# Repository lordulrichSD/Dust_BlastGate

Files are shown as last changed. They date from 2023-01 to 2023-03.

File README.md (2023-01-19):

# Dust_BlastGate

This project is a Dust collection system blast gate for woodworking or other dust collection.  The device provides control of a servo to actuate the blast gate, manual control of the blast gate position, a connector to attatch a sensor for tool activation and automatic control and wifi connection to activate a dust collector connected to a Kassa capable smart plug or switch.  

Software is seetup to allow over the air firmware updates direct from github. BoardInfo.py and Settings.py are not part of OTA update. BoardInfo.py contains hardware pinouts and should reflect hardware revisions.  Settings.py contains device configurations, i.e. wifi, servo limits, IP for dust collector and delay time.  These settings are set per device

BoardInfo files contain board specific information (i.e. pin mappings), BoardInfo must be loaded manualy at inital install and will not update OTA.  

Hardware folder contains KiCAD files for board revisions.  Boards are uploaded to OSHpark.  

Firmware folder contains the firmware.  Files except Settings.py are subject to OTA update.  

settings.py file contains example data/startup data. File will be overwritten when configuring board for the first time.  Write this file durring intial install.

Hardware
Hardware contains 2 main modules.  The main control module and sensor module.  
The main control module contains an ESP32 module (providing microcontroler and wifi connection).  In addition the main control module holds support hardware (i.e. power supply) and interface connections.  
A manual control switch (1p3t on-off-on) provides manual on, auto, manual off control.  
Dip switches provide for entering Access Point Mode for settings, enabling WIFI (when not in AP mode) enabling the sensor in put.  
A FTDI type 6 pin headder is provided for programing and debug by serial.
A 3 pin header is provided to connect a hobby servo to activate the physical blast gate
Sensor connection is via a RJ-9 Style connector to allow easy cable creation of needed lenght for indivitual physical install.  This connector includes 3.3v, ground, sensor data (logic high/low), and raw USB voltage (allowing USB power supply to be at sensor location)
A USB connetor is provided for power only.  A jumper or switch (populate 1) allowing selection of power source (one at a time, sensor or main control module)

(Future feature to deploy)
OTA updated based on ugit (https://github.com/turfptax/ugit)
https://github.com/turfptax/ugit/blob/f6872930eea33ae5fb45ea48af146518e4737e93/ugit.py

KASA integration based on the work by GadgetReactor in the pyHS100 based on the work of The communication protocol was reverse engineered by Lubomir Stroetmann and
Tobias Esser in 'Reverse Engineering the TP-Link HS110':
https://www.softscheck.com/en/reverse-engineering-tp-link-hs110/.  The HS100 or python-kasa libraries were not used directly due to memory limitations of the ESP32 module so only limited functions were recreated directly.

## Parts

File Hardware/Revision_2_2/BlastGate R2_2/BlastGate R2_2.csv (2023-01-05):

Source: | C:\Users\Catherine\Documents\BlastGate\BlastGate R2\BlastGate R2.kicad_sch
Date: | 11/16/2022 3:56:45 PM
Tool: | Eeschema (6.0.7)
Generator: | C:\Program Files\KiCad\6.0\bin\scripting\plugins/bom_csv_grouped_by_value_with_fp.py
Component Count: | 40
Ref | Qnty | Value | Cmp name | Footprint | Description | Vendor
C2, C6, C7, C9, | 4 | 0.1uf | C | Capacitor_SMD:C_1206_3216Metric_Pad1.33x1.80mm_HandSolder | Unpolarized capacitor
C3, C4, C12, C13, | 4 | 100uf | C_Polarized | Capacitor_THT:CP_Radial_D5.0mm_P2.50mm | Polarized capacitor
C5, C8, C10, | 3 | 1000uf | C_Polarized | Capacitor_THT:CP_Radial_D12.5mm_P5.00mm | Polarized capacitor
C11, | 1 | 1uf | C | Capacitor_SMD:C_1206_3216Metric_Pad1.33x1.80mm_HandSolder | Unpolarized capacitor
D1, D2, D3, D4, D5, | 5 | LED | LED | LED_SMD:LED_1206_3216Metric_Pad1.42x1.75mm_HandSolder | Light emitting diode
D6, | 1 | D | D | Diode_THT:D_DO-41_SOD81_P7.62mm_Horizontal | Diode
J1, | 1 | Conn_01x03_Male | Conn_01x03_Male | Connector_PinHeader_2.54mm:PinHeader_1x03_P2.54mm_Vertical | Generic connector, single row, 01x03, script generated (kicad-library-utils/schlib/autogen/connector/)
J2, | 1 | Conn_01x06_Male | Conn_01x06_Male | Connector_PinHeader_2.54mm:PinHeader_1x06_P2.54mm_Vertical | Generic connector, single row, 01x06, script generated (kicad-library-utils/schlib/autogen/connector/)
J3, | 1 | USB_B_Micro | USB_B_Micro | Connector_USB:USB_Micro-B_Amphenol_10118194_Horizontal | USB Micro Type B connector
J4, | 1 | RJ9 | RJ9 | projectLib:modjack | RJ connector, 4P4C (4 positions 4 connected)
POWSEL1, | 1 | SW_SPDT | SW_SPDT | projectLib:EG1224 | Switch, single pole double throw
PROG1, | 1 | SW_Push | SW_Push | projectLib:pb | Push button switch, generic, two pins
R1, R2, R3, R4, R5, R6, R7, R8, R9, R10, R11, | 11 | 10K | R | Resistor_SMD:R_1206_3216Metric_Pad1.30x1.75mm_HandSolder | Resistor
RST1, | 1 | SW_Push | SW_Push | projectLib:pb | Push button switch, generic, two pins
SW1, | 1 | SW_DIP_x03 | SW_DIP_x03 | Button_Switch_THT:SW_DIP_SPSTx03_Slide_6.7x9.18mm_W7.62mm_P2.54mm_LowProfile | 3x DIP Switch, Single Pole Single Throw (SPST) switch, small symbol
SW2, | 1 | SW_SPDT_MSM | SW_SPDT_MSM | Button_Switch_THT:SW_Slide_1P2T_CK_OS102011MS2Q | Switch, single pole double throw, center OFF position
U1, | 1 | AP2112M-3.3 | AP2112K-3.3 | Package_SO:Diodes_SO-8EP | 600mA low dropout linear regulator, with enable pin, 3.8V-6V input voltage range, 3.3V fixed positive output, SOT-23-5
U2, | 1 | ESP32-WROOM-32D | ESP32-WROOM-32D | RF_Module:ESP32-WROOM-32 | RF Module, ESP32-D0WD SoC, Wi-Fi 802.11b/g/n, Bluetooth, BLE, 32-bit, 2.7-3.6V, onboard antenna, SMD

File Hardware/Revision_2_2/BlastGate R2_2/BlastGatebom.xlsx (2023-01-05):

Source: | C:\Users\Catherine\Documents\BlastGate\BlastGate R2\BlastGate R2.kicad_sch
Date: | 2022-10-18 19:58
Tool: | Eeschema (6.0.7)
Generator: | C:\Program Files\KiCad\6.0\bin\scripting\plugins/bom_csv_grouped_by_value_with_fp.py
Component Count: | 40
Ref | Qnty | Value | Footprint | Description | Vendor
SW3, SW4, | 2 | SW_Push | Button_Switch_SMD:SW_Push_1P1T_NO_CK_KMR2 | Push button switch, generic, two pins
SW2, | 1 | SW_SPDT_MSM | Button_Switch_THT:SW_Slide_1P2T_CK_OS102011MS2Q | Switch, single pole double throw, center OFF position
C1, | 1 | 10uf | Capacitor_SMD:C_0805_2012Metric_Pad1.18x1.45mm_HandSolder | Unpolarized capacitor
C2, C3, | 2 | 1uf | Capacitor_SMD:C_0805_2012Metric_Pad1.18x1.45mm_HandSolder | Unpolarized capacitor
C4, C5, | 2 | C | Capacitor_SMD:C_0805_2012Metric_Pad1.18x1.45mm_HandSolder | Unpolarized capacitor
C6, | 1 | .002uf | Capacitor_SMD:C_0805_2012Metric_Pad1.18x1.45mm_HandSolder | Unpolarized capacitor
C7, | 1 | .1uf | Capacitor_SMD:C_0805_2012Metric_Pad1.18x1.45mm_HandSolder | Unpolarized capacitor
C8, C9, C10, | 3 | .22uf | Capacitor_SMD:C_0805_2012Metric_Pad1.18x1.45mm_HandSolder | Unpolarized capacitor
C2, C6, C7, C9, | 4 | 0.1uf | Capacitor_SMD:C_1206_3216Metric_Pad1.33x1.80mm_HandSolder | Unpolarized capacitor
C11, | 1 | 1uf | Capacitor_SMD:C_1206_3216Metric_Pad1.33x1.80mm_HandSolder | Unpolarized capacitor
C5, C8, C10, | 3 | 1000uf | Capacitor_THT:CP_Radial_D12.5mm_P5.00mm | Polarized capacitor
C3, C4, C12, C13, | 4 | 100uf | Capacitor_THT:CP_Radial_D5.0mm_P2.50mm | Polarized capacitor
J1, | 1 | Conn_01x03_Male | Connector_PinHeader_2.54mm:PinHeader_1x03_P2.54mm_Vertical | Generic connector, single row, 01x03, script generated (kicad-library-utils/schlib/autogen/connector/)
J2, | 1 | Conn_01x06_Male | Connector_PinHeader_2.54mm:PinHeader_1x06_P2.54mm_Vertical | Generic connector, single row, 01x06, script generated (kicad-library-utils/schlib/autogen/connector/)
J4, | 1 | RJ9 | Connector_RJ:RJ14_Connfly_DS1133-S4_Horizontal | RJ connector, 4P4C (4 positions 4 connected)
J2, | 1 | RJ9 | Connector_RJ:RJ14_Connfly_DS1133-S4_Horizontal | RJ connector, 4P4C (4 positions 4 connected)
J3, | 1 | USB_B_Micro | Connector_USB:USB_Micro-B_Wuerth_629105150521_CircularHoles | USB Micro Type B connector
J1, | 1 | USB_B_Micro | Connector_USB:USB_Micro-B_Wuerth_629105150521_CircularHoles | USB Micro Type B connector
D1, D2, | 2 | D | Diode_SMD:D_SOD-123 | Diode
D6, | 1 | D | Diode_THT:D_DO-41_SOD81_P7.62mm_Horizontal | Diode
D1, D2, D3, D4, D5, | 5 | LED | LED_SMD:LED_1206_3216Metric_Pad1.42x1.75mm_HandSolder | Light emitting diode
D3, | 1 | LED | LED_SMD:LED_1206_3216Metric_Pad1.42x1.75mm_HandSolder | Light emitting diode
SW1, | 1 | SW_DIP_x03 | Package_DIP:DIP-6_W10.16mm | 3x DIP Switch, Single Pole Single Throw (SPST) switch, small symbol
U1, | 1 | AP2112M-3.3 | Package_SO:Diodes_SO-8EP | 600mA low dropout linear regulator, with enable pin, 3.8V-6V input voltage range, 3.3V fixed positive output, SOT-23-5
U3, | 1 | TLV9104 | Package_SO:TSSOP-14_4.4x5mm_P0.65mm
U1, U2, | 2 | A1302ELHLT-T | Package_TO_SOT_SMD:SOT-23W | Linear Hall Effect Sensor, SOT-23W
U4, | 1 | TLV9101 | Package_TO_SOT_SMD:SOT-353_SC-70-5_Handsoldering
RV1, RV2, RV3, | 3 | R_Potentiometer_Small | Potentiometer_THT:Potentiometer_Bourns_3266Y_Vertical | Potentiometer
SW5, | 1 | SW_SPDT | projectLib:EG1224 | Switch, single pole double throw
R1, R2, R3, R4, R5, R6, R7, R8, R9, R10, R11, | 11 | 10K | Resistor_SMD:R_1206_3216Metric_Pad1.30x1.75mm_HandSolder | Resistor
R1, R2, R8, R9, | 4 | 100K | Resistor_SMD:R_1206_3216Metric_Pad1.30x1.75mm_HandSolder | Resistor
R3, R4, R10, | 3 | 4.99K | Resistor_SMD:R_1206_3216Metric_Pad1.30x1.75mm_HandSolder | Resistor
R5, R6, | 2 | 300K | Resistor_SMD:R_1206_3216Metric_Pad1.30x1.75mm_HandSolder | Resistor
R7, | 1 | 1M | Resistor_SMD:R_1206_3216Metric_Pad1.30x1.75mm_HandSolder | Resistor
R11, | 1 | 100M | Resistor_SMD:R_1206_3216Metric_Pad1.30x1.75mm_HandSolder | Resistor
R12, R13, R14, | 3 | R | Resistor_SMD:R_1206_3216Metric_Pad1.30x1.75mm_HandSolder | Resistor
U2, | 1 | ESP32-WROOM-32D | RF_Module:ESP32-WROOM-32 | RF Module, ESP32-D0WD SoC, Wi-Fi 802.11b/g/n, Bluetooth, BLE, 32-bit, 2.7-3.6V, onboard antenna, SMD

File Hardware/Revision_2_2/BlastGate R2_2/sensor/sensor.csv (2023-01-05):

Source: | C:\Users\Catherine\Documents\BlastGate\BlastGate R2\sensor\sensor.kicad_sch
Date: | 11/16/2022 3:57:41 PM
Tool: | Eeschema (6.0.7)
Generator: | C:\Program Files\KiCad\6.0\bin\scripting\plugins/bom_csv_grouped_by_value_with_fp.py
Component Count: | 36
Ref | Qnty | Value | Cmp name | Footprint | Description | Vendor
C1, | 1 | 10uf | C | Capacitor_SMD:C_0805_2012Metric_Pad1.18x1.45mm_HandSolder | Unpolarized capacitor
C2, C3, | 2 | 1uf | C | Capacitor_SMD:C_0805_2012Metric_Pad1.18x1.45mm_HandSolder | Unpolarized capacitor
C4, C5, | 2 | C | C | Capacitor_SMD:C_0805_2012Metric_Pad1.18x1.45mm_HandSolder | Unpolarized capacitor
C6, | 1 | .002uf | C | Capacitor_SMD:C_0805_2012Metric_Pad1.18x1.45mm_HandSolder | Unpolarized capacitor
C7, | 1 | .1uf | C | Capacitor_SMD:C_0805_2012Metric_Pad1.18x1.45mm_HandSolder | Unpolarized capacitor
C8, C9, C10, | 3 | .22uf | C | Capacitor_SMD:C_0805_2012Metric_Pad1.18x1.45mm_HandSolder | Unpolarized capacitor
D1, D2, | 2 | D | D | Diode_SMD:D_SOD-123 | Diode
D3, | 1 | LED | LED | LED_SMD:LED_1206_3216Metric_Pad1.42x1.75mm_HandSolder | Light emitting diode
J1, | 1 | USB_B_Micro | USB_B_Micro | Connector_USB:USB_Micro-B_Amphenol_10118194_Horizontal | USB Micro Type B connector
J2, | 1 | RJ9 | RJ9 | projlib:modjack | RJ connector, 4P4C (4 positions 4 connected)
R1, R2, R8, R9, | 4 | 100K | R | Resistor_SMD:R_1206_3216Metric_Pad1.30x1.75mm_HandSolder | Resistor
R3, R4, R10, | 3 | 4.99K | R | Resistor_SMD:R_1206_3216Metric_Pad1.30x1.75mm_HandSolder | Resistor
R5, R6, | 2 | 300K | R | Resistor_SMD:R_1206_3216Metric_Pad1.30x1.75mm_HandSolder | Resistor
R7, | 1 | 1M | R | Resistor_SMD:R_1206_3216Metric_Pad1.30x1.75mm_HandSolder | Resistor
R11, | 1 | 100M | R | Resistor_SMD:R_1206_3216Metric_Pad1.30x1.75mm_HandSolder | Resistor
R12, R13, R14, | 3 | R | R | Resistor_SMD:R_1206_3216Metric_Pad1.30x1.75mm_HandSolder | Resistor
RV1, RV2, RV3, | 3 | R_Potentiometer_Small | R_Potentiometer_Small | Potentiometer_SMD:Potentiometer_Bourns_TC33X_Vertical | Potentiometer
U1, U2, | 2 | A1302ELHLT-T | A1302ELHLT-T | Package_TO_SOT_THT:TO-92L_Inline | Linear Hall Effect Sensor, SOT-23W
U3, | 1 | TLV9104 | TLV9104 | Package_SO:TSSOP-14_4.4x5mm_P0.65mm
U4, | 1 | TLV9101 | TLV9101 | Package_TO_SOT_SMD:SOT-353_SC-70-5_Handsoldering

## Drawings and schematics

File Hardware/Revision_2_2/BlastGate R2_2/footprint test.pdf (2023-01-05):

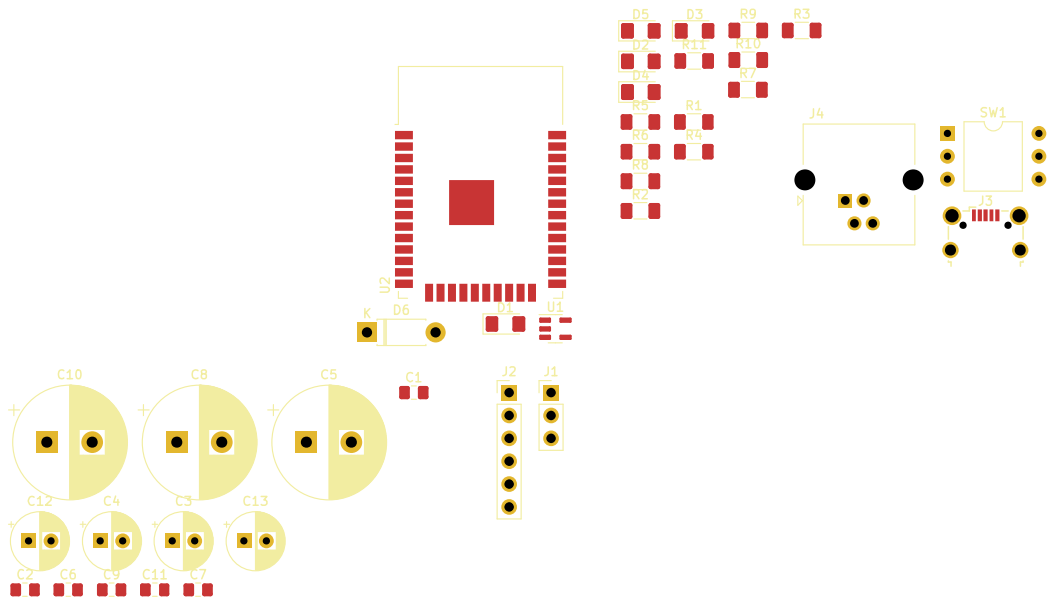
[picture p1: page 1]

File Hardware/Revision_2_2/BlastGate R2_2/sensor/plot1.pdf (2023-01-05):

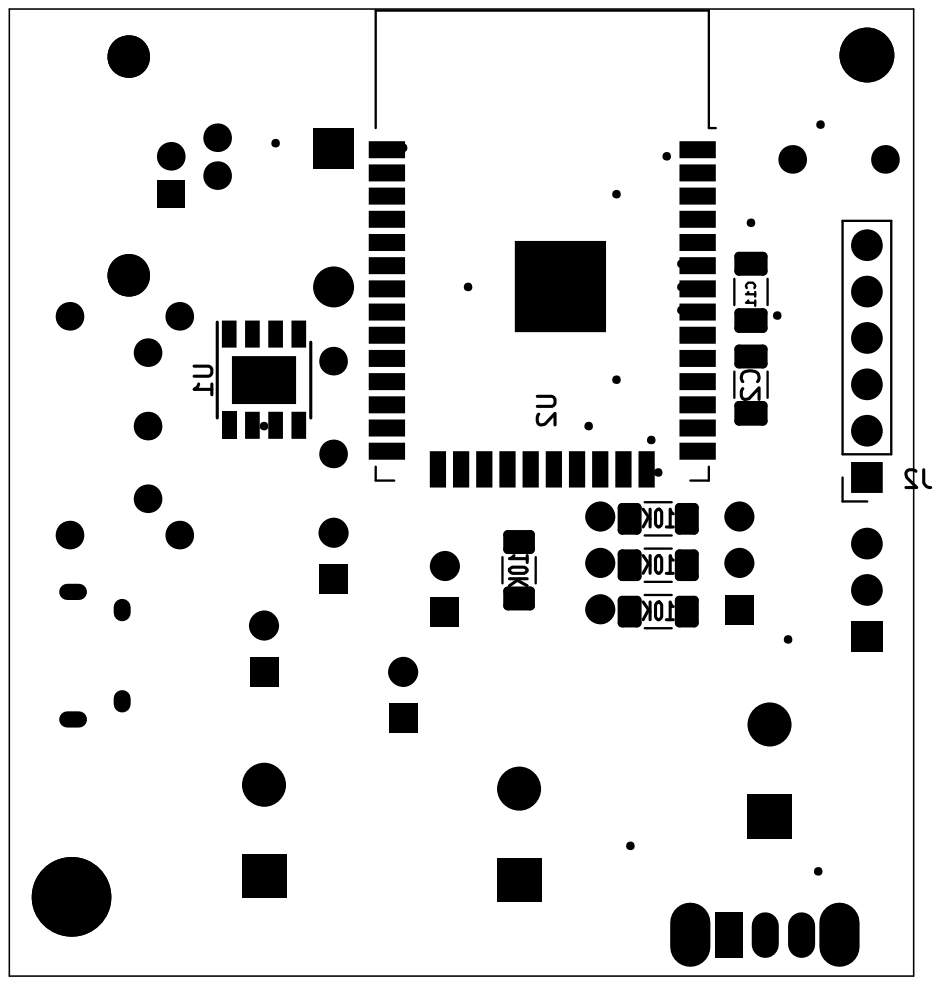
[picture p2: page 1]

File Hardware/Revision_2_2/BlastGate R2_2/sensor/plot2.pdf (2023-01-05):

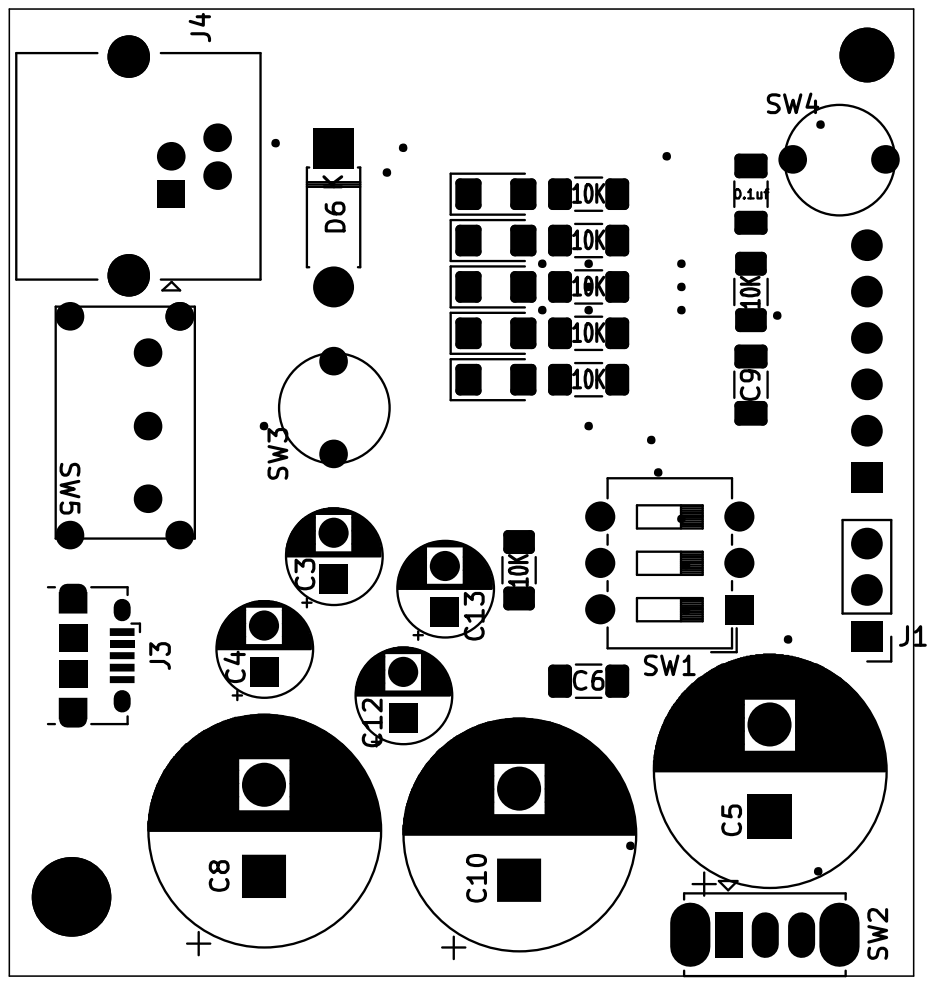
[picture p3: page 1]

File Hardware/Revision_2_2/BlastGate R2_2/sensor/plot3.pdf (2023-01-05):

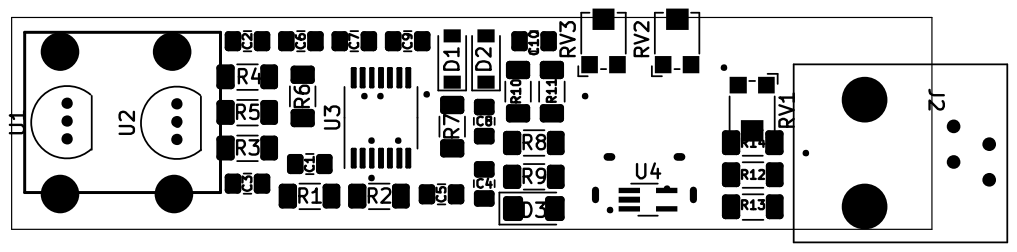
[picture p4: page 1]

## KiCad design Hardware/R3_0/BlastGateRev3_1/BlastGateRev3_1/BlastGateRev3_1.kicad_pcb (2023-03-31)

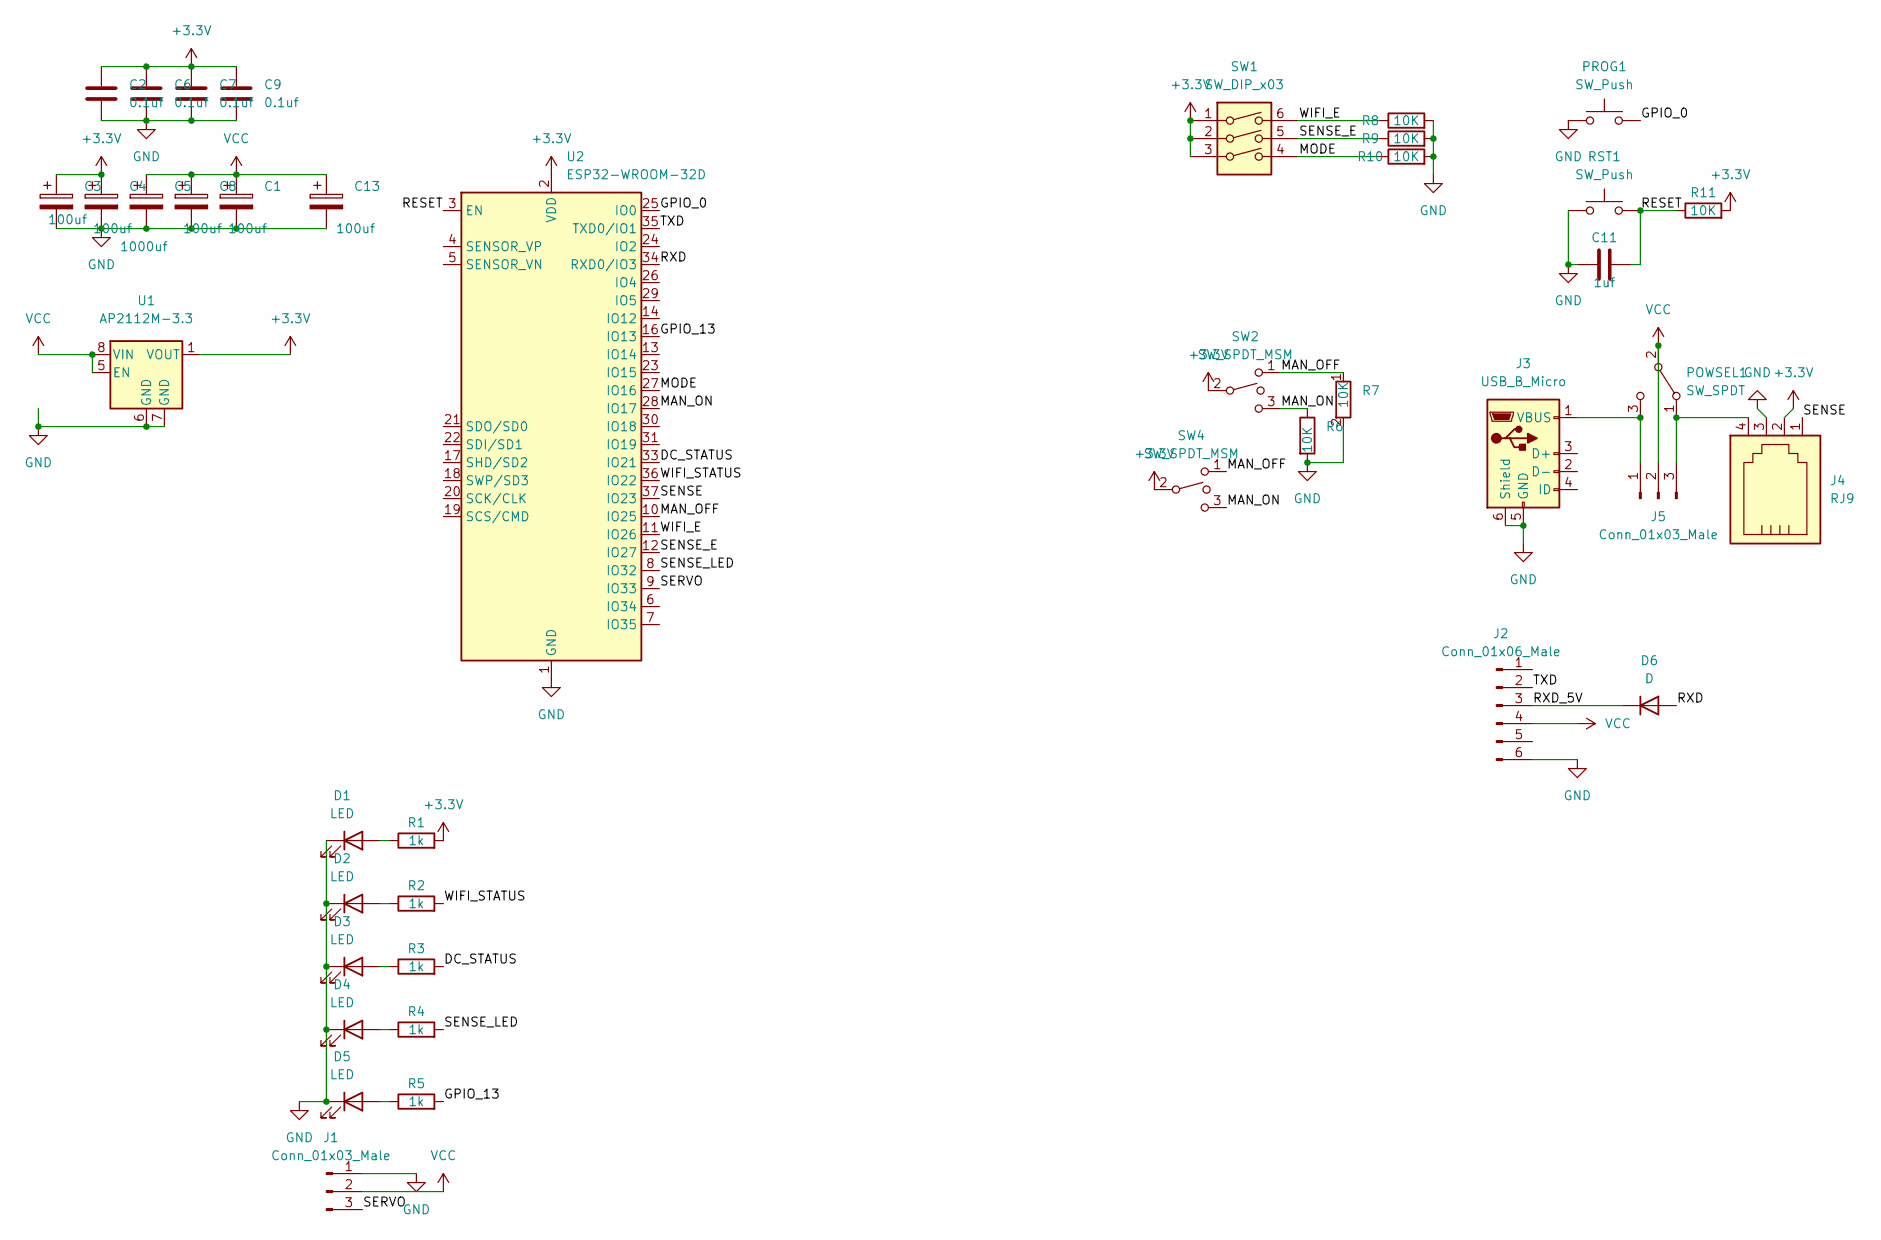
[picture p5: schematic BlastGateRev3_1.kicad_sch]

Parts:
C1, C3, C4, C8, C13: 100uf; CP_Radial_D5.0mm_P2.50mm
C2, C6, C7, C9: 0.1uf; C_1206_3216Metric_Pad1.33x1.80mm_HandSolder
C5: 1000uf; CP_Radial_D12.5mm_P5.00mm
C11: 1uf; C_1206_3216Metric_Pad1.33x1.80mm_HandSolder
D1, D2, D3, D4, D5: LED; LED_1206_3216Metric_Pad1.42x1.75mm_HandSolder
D6: D; D_DO-41_SOD81_P3.81mm_Vertical_AnodeUp
J1, J5: Conn_01x03_Male; PinHeader_1x03_0.1in lock
J2: Conn_01x06_Male; PinHeader_1x06, .1in Lock
J3: USB_B_Micro; usb; PartNum 54-00019T-ND
J4: RJ9; modjack; PartNum AE10381-ND
POWSEL1: SW_SPDT; EG1224
PROG1: SW_Push; pb CKN12301-ND; PartNum CKN12301-ND
R1, R2, R3, R4, R5: 1k; R_1206_3216Metric_Pad1.30x1.75mm_HandSolder
R6, R7, R8, R9, R10, R11: 10K; R_1206_3216Metric_Pad1.30x1.75mm_HandSolder
RST1: SW_Push; pb CKN12301-ND; PartNum CKN12301-ND
SW1: SW_DIP_x03; SW_DIP_SPSTx03_Slide_6.7x9.18mm_W7.62mm_P2.54mm_LowProfile; PartNum CT2103MS-ND
SW2: SW_SPDT_MSM; BST13T1AVR; PartNum 2449-BST13T1AVR-ND
SW4: SW_SPDT_MSM; 400AWMSP3R1BLKM6QE rocker; PartNum 400AWMSP3R1BLKM6QE-ND
U1: AP2112M-3.3; Diodes_SO-8EP; PartNum AP2112M-3.3TRG1DICT-ND
U2: ESP32-WROOM-32D; ESP32-WROOM-32; PartNum 1965-ESP32-WROOM-32E-H4CT-ND

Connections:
+3.3V: C2.1, C3.1, C4.1, C6.1, C7.1, C9.1, J4.2, R1.2, R11.2, SW1.1, SW1.2, SW1.3, SW2.2, SW4.2, U1.1 (VOUT), U2.2 (VDD)
/DC_STATUS: R3.2, U2.33 (IO21)
/GPIO_0: PROG1.2, U2.25 (IO0)
/GPIO_13: R5.2, U2.16 (IO13)
/MAN_OFF: R7.1, SW2.1, SW4.1, U2.10 (IO25)
/MAN_ON: R6.1, SW2.3, SW4.3, U2.28 (IO17)
/MODE: R10.1, SW1.4, U2.27 (IO16)
/RESET: C11.2, R11.1, RST1.2, U2.3 (EN)
/RXD: D6.2 (A), U2.34 (RXD0/IO3)
/RXD_5V: D6.1 (K), J2.3
/SENSE: J4.1, U2.37 (IO23)
/SENSE_E: R9.1, SW1.5, U2.12 (IO27)
/SENSE_LED: R4.2, U2.8 (IO32)
/SERVO: J1.3, U2.9 (IO33)
/TXD: J2.2, U2.35 (TXD0/IO1)
/WIFI_E: R8.1, SW1.6, U2.11 (IO26)
/WIFI_STATUS: R2.2, U2.36 (IO22)
GND: C1.2, C2.2, C3.2, C4.2, C5.2, C6.2, C7.2, C8.2, C9.2, C11.1, C13.2, D1.1 (K), D2.1 (K), D3.1 (K), D4.1 (K), D5.1 (K), J1.1, J2.6, J3.5 (GND), J3.6 (Shield), J4.3, PROG1.1, R6.2, R7.2, R8.2, R9.2, R10.2, RST1.1, U1.6 (GND), U1.7 (GND), U2.1 (GND), U2.15 (GND), U2.38 (GND), U2.39 (GND)
unnamed: D1.2 (A), R1.1
unnamed: D2.2 (A), R2.1
unnamed: D3.2 (A), R3.1
unnamed: D4.2 (A), R4.1
unnamed: D5.2 (A), R5.1
unnamed: J3.1 (VBUS), J5.1, POWSEL1.3 (C)
unnamed: J4.4, J5.3, POWSEL1.1 (A)
VCC: C1.1, C5.1, C8.1, C13.1, J1.2, J2.4, J5.2, POWSEL1.2 (B), U1.5 (EN), U1.8 (VIN)

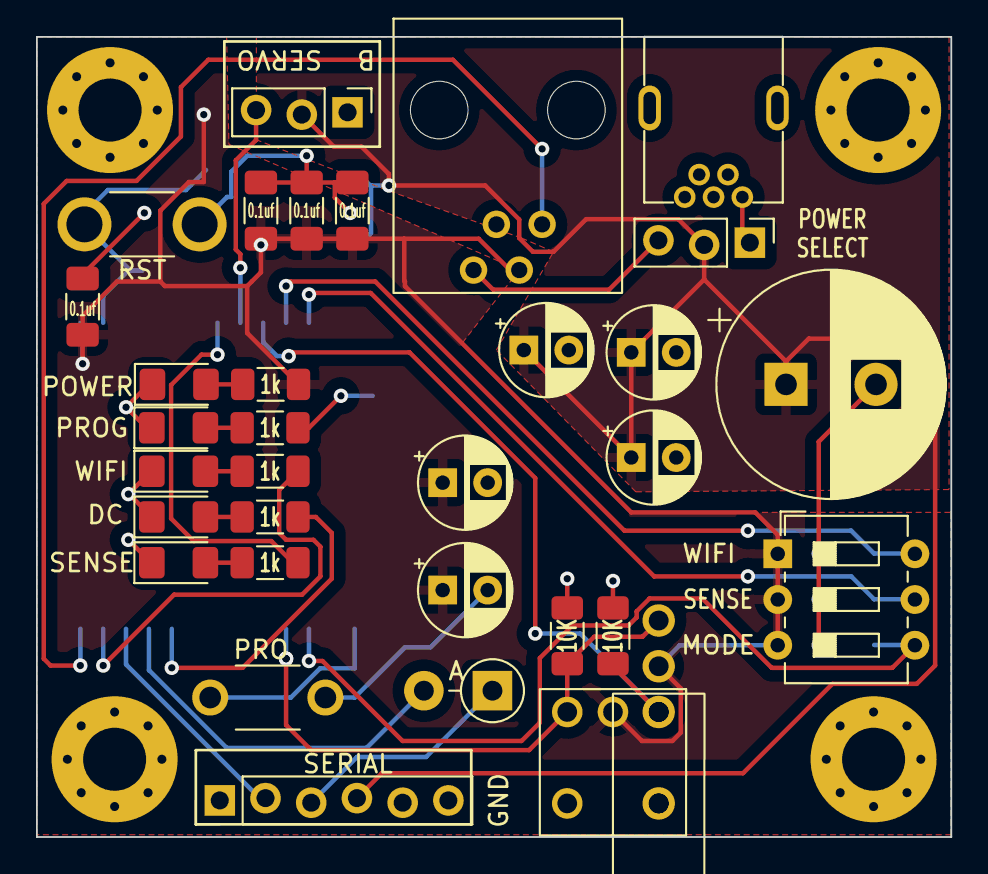
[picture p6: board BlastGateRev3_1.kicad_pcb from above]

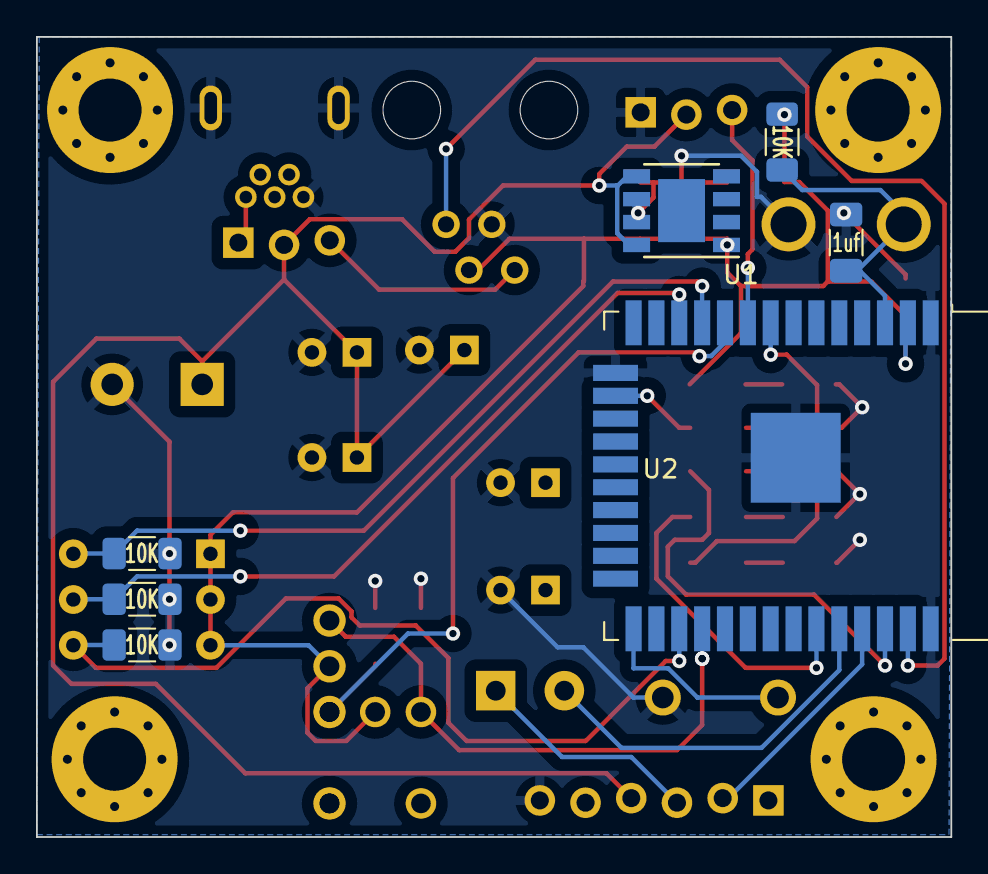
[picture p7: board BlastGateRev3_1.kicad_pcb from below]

Board: 2 copper layers, 50.8 x 44.5 mm, 40 parts (7 on the bottom side), 26 nets.

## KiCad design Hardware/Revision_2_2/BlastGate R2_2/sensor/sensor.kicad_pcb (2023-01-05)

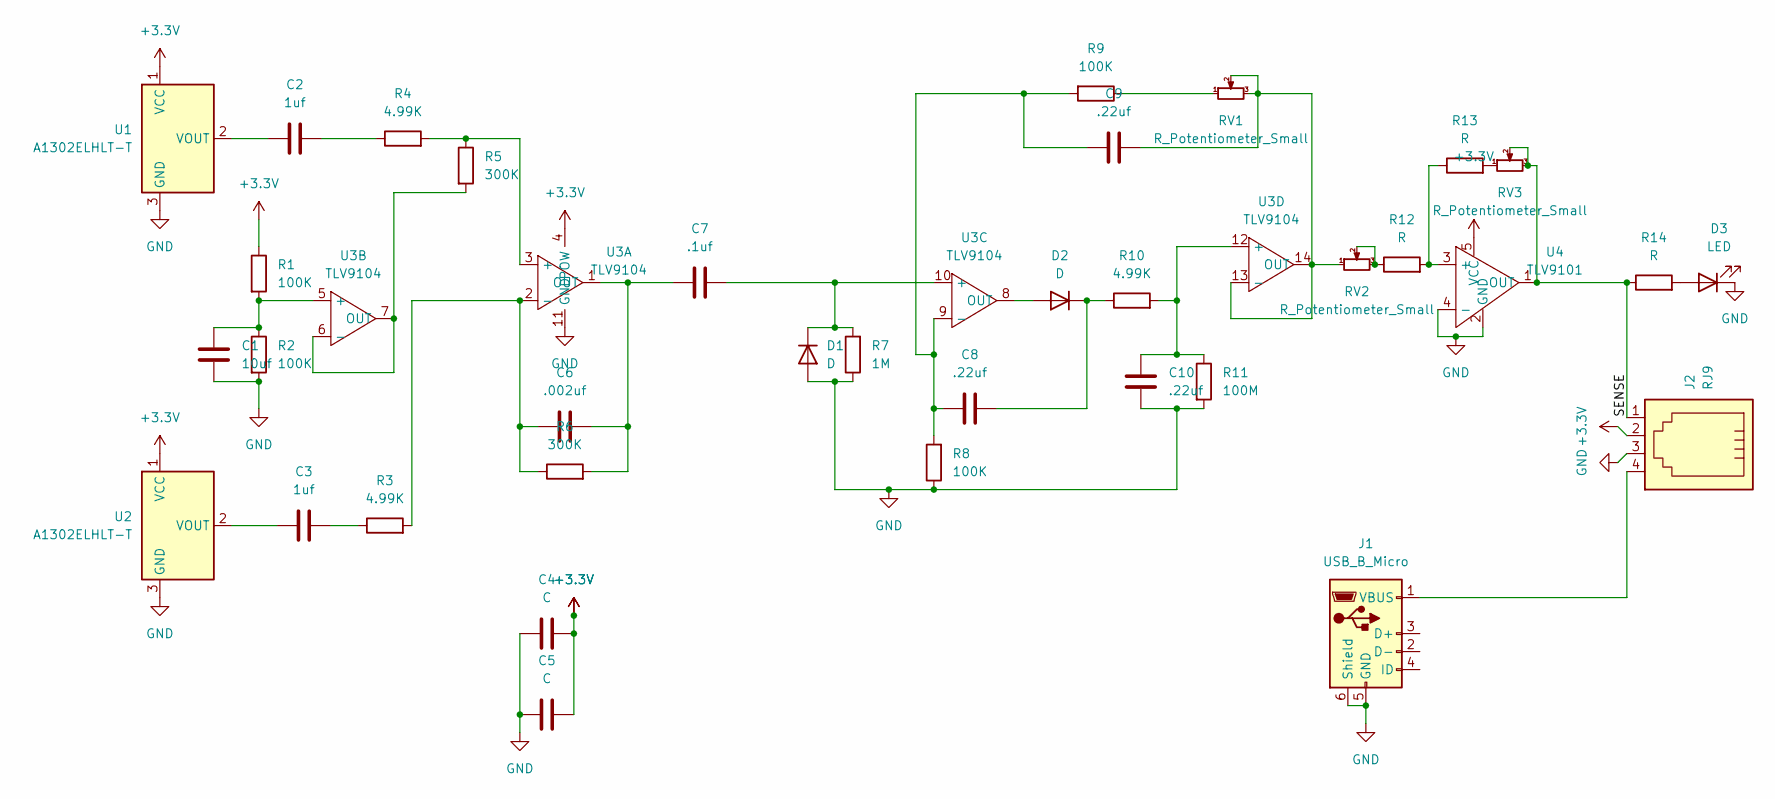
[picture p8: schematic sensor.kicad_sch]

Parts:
C1: 10uf; C_0805_2012Metric_Pad1.18x1.45mm_HandSolder
C2, C3: 1uf; C_0805_2012Metric_Pad1.18x1.45mm_HandSolder
C4, C5: C; C_0805_2012Metric_Pad1.18x1.45mm_HandSolder
C6: .002uf; C_0805_2012Metric_Pad1.18x1.45mm_HandSolder
C7: .1uf; C_0805_2012Metric_Pad1.18x1.45mm_HandSolder
C8, C9, C10: .22uf; C_0805_2012Metric_Pad1.18x1.45mm_HandSolder
D1, D2: D; D_SOD-123
D3: LED; LED_1206_3216Metric_Pad1.42x1.75mm_HandSolder
J1: USB_B_Micro; USB_Micro-B_Amphenol_10118194_Horizontal
J2: RJ9; modjack
R1, R2, R8, R9: 100K; R_1206_3216Metric_Pad1.30x1.75mm_HandSolder
R3, R4, R10: 4.99K; R_1206_3216Metric_Pad1.30x1.75mm_HandSolder
R5, R6: 300K; R_1206_3216Metric_Pad1.30x1.75mm_HandSolder
R7: 1M; R_1206_3216Metric_Pad1.30x1.75mm_HandSolder
R11: 100M; R_1206_3216Metric_Pad1.30x1.75mm_HandSolder
R12, R13, R14: R; R_1206_3216Metric_Pad1.30x1.75mm_HandSolder
RV1, RV2, RV3: R_Potentiometer_Small; Potentiometer_Bourns_TC33X_Vertical
U1, U2: A1302ELHLT-T; TO-92L_Inline
U3: TLV9104; TSSOP-14_4.4x5mm_P0.65mm
U4: TLV9101; SOT-353_SC-70-5_Handsoldering

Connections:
+3.3V: C4.2, C5.2, J2.2, R1.1, U1.1 (VCC), U2.1 (VCC), U3.4 (POW), U4.5 (VCC)
/SENSE: J2.1, R14.1, RV3.2, RV3.3, U4.1 (OUT)
GND: C1.2, C4.1, C5.1, C10.1, D1.2 (A), D3.1 (K), J1.5 (GND), J1.6 (Shield), J2.3, R2.2, R7.1, R8.1, R11.2, U1.3 (GND), U2.3 (GND), U3.11 (GND), U4.2 (GND), U4.4 (-)
unnamed: C1.1, R1.2, R2.1, U3.5 (+)
unnamed: C2.1, R4.1
unnamed: C2.2, U1.2 (VOUT)
unnamed: C3.1, U2.2 (VOUT)
unnamed: C3.2, R3.1
unnamed: C6.1, R3.2, R6.1, U3.2 (-)
unnamed: C6.2, C7.1, R6.2, U3.1 (OUT)
unnamed: C7.2, D1.1 (K), R7.2, U3.10 (+)
unnamed: C8.1, C9.2, R8.2, R9.2, U3.9 (-)
unnamed: C8.2, D2.1 (K), R10.1
unnamed: C9.1, RV1.2, RV1.3, RV2.1, U3.13 (-), U3.14 (OUT)
unnamed: C10.2, R10.2, R11.1, U3.12 (+)
unnamed: D2.2 (A), U3.8 (OUT)
unnamed: D3.2 (A), R14.2
unnamed: J1.1 (VBUS), J2.4
unnamed: R4.2, R5.1, U3.3 (+)
unnamed: R5.2, U3.6 (-), U3.7 (OUT)
unnamed: R9.1, RV1.1
unnamed: R12.1, RV2.2, RV2.3
unnamed: R12.2, R13.1, U4.3 (+)
unnamed: R13.2, RV3.1

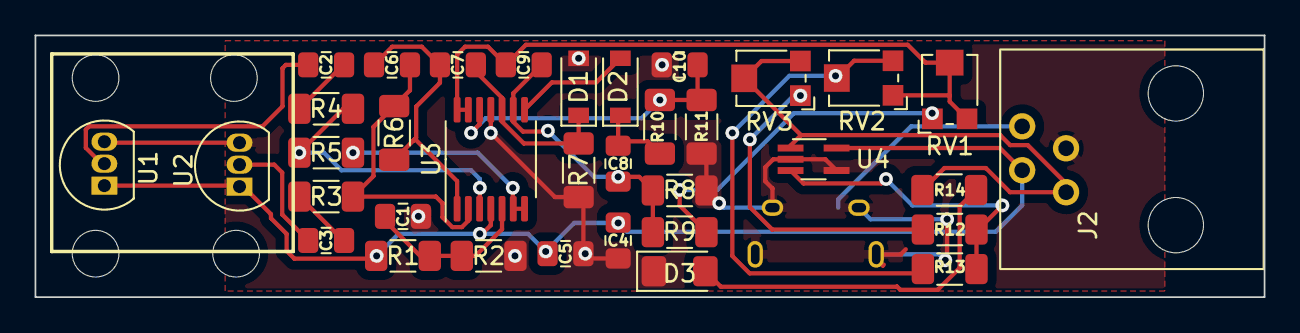
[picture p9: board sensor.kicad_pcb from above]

Board: 2 copper layers, 71.1 x 15.1 mm, 36 parts (1 on the bottom side), 24 nets.

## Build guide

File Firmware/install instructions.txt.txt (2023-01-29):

Install micropython on the board

Load the folloing onto the board
	APmode.py
	boot.py
	main.py
	Settings.py- you may want to modify this file to inclue you SSID, password and other inital settings
	BoardInfo.py  - Use file aproprae for version of hardware located in BoardInfo directory

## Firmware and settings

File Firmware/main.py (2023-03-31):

##Import libraries

import machine
try:
  import usocket as socket
except:
  import socket
import network
import time
from struct import pack
import gc

#BoardInfo.py contains hardware specific information (i.e. pinouts, constant per hardware revision but may change with upddated hardware
import BoardInfo
#Settings.py containd device specific informaton (i.e. wifi configuration, open and closed positions and delay time)
import Settings

gc.enable()

#define Variables - grab data from Settings.py configuration file
SSID = Settings.SSID
password = Settings.password
DCIP= Settings.DCIP
closedPos=Settings.closedPos
openPos= Settings.openPos
delayTime=Settings.delayTime
delay2=Settings.delay2



#define functions


#Setup pins
#setup pins
modeP = machine.Pin(BoardInfo.modePin, machine.Pin.IN)      
senseP =  machine.Pin(BoardInfo.sensePin, machine.Pin.IN)
manOnP = machine.Pin(BoardInfo.manOnPin, machine.Pin.IN)
manOffP = machine.Pin(BoardInfo.manOffPin, machine.Pin.IN)
wifiEnP = machine.Pin(BoardInfo.wifiEnPin, machine.Pin.IN)
senseEnP = machine.Pin(BoardInfo.senseEnPin, machine.Pin.IN)


#Led pins, set to off
dcStatusP = machine.Pin(BoardInfo.dcStatusPin, machine.Pin.OUT)
dcStatusP.value(0)

senseStatusP = machine.Pin(BoardInfo.senseStatusPin, machine.Pin.OUT)
senseStatusP.value(0)

wifiStatusP = machine.Pin(BoardInfo.wifiStatusPin, machine.Pin.OUT)
wifiStatusP.value(0)

##Check Mode
if (modeP.value()==1):
    import APmode
    APmode.run()


#setup sero
servoP=machine.Pin(BoardInfo.servoPin, machine.Pin.OUT)
servo = machine.PWM(servoP,freq=50)
print("closing servo")
servoSet(closedPos)

if wifiEnP():
    #check if WIFI Enabled and if so try to connect    
    WIFI = network.WLAN(network.STA_IF)
    connectWIFI()
    wifiStatusP.value(WIFI.isconnected())


on=False

#Go to loop
while (True):
    if wifiEnP():
        if WIFI.isconnected():
            wifiStatusP.value(1)
            #print("DC Status Value")
            #print(getStatus())
            if getStatus() == "1":
                dcStatusP.value(1)
                print("Dust Collector On")
            else:
                dcStatusP.value(0)
                print("Dust Collector Off")
        else:
            connectWIFI()
            wifiStatusP.value(WIFI.isconnected())
    
    #Sense operating position
    if manOnP.value():
        #Manual On
        print("Manual On")
        #if on==False:
        
        TurnOnDC()          
        on = True

    elif manOffP.value():
        print("Manual Off")
        if on==True:
            time.sleep(delayTime)
            TurnOffDC()
                
        on = False
        
    elif senseEnP.value():
        print("Auto Sense")
        
        if senseP.value():
            print("Auto On")
            senseStatusP.value(1)
            #if on==False:
            TurnOnDC()          
            on = True
        else:
            print("Auto Off")
            senseStatusP.value(0)
            if on==True:
                time.sleep(delayTime)
                TurnOffDC()
            on = False           

    gc.collect()
    now=time.localtime()
    if now[3]==0:
        if time.time()>3600
            TurnOffDC()
            machine.rest()
    time.sleep_ms(10)
    

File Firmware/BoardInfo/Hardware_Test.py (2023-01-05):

#hardware test program for blast gate
#This program to test board assembly, will flaxh LEDs, run servo limit to limit and then print inputs to the serial port

import machine
import time

import BoardInfo


closedPos=0
openPos=100

def servoSet(pos):
    #sets servo, to value between 0 and 100
    posA = min(max(0, pos),100)
    outval=int(posA*.75)+40
    servo.duty(outval)
    #print(outval)     

#Setup pins
#setup pins
modeP = machine.Pin(BoardInfo.modePin, machine.Pin.IN)      
senseP =  machine.Pin(BoardInfo.sensePin, machine.Pin.IN)
manOnP = machine.Pin(BoardInfo.manOnPin, machine.Pin.IN)
manOffP = machine.Pin(BoardInfo.manOffPin, machine.Pin.IN)
wifiEnP = machine.Pin(BoardInfo.wifiEnPin, machine.Pin.IN)
senseEnP = machine.Pin(BoardInfo.senseEnPin, machine.Pin.IN)



#Led pins, set to off
dcStatusP = machine.Pin(BoardInfo.dcStatusPin, machine.Pin.OUT)
dcStatusP.value(0)

progP= machine.Pin(13, machine.Pin.OUT)
progP.value(0)

senseStatusP = machine.Pin(BoardInfo.senseStatusPin, machine.Pin.OUT)
senseStatusP.value(0)

wifiStatusP = machine.Pin(BoardInfo.wifiStatusPin, machine.Pin.OUT)
wifiStatusP.value(0)

def lights(v):
    wifiStatusP.value(v)
    senseStatusP.value(v)
    dcStatusP.value(v)
    progP.value(v)

print("Blast Gate Hardware Test")
print("Servo Test - Servo Sweeps 10 Seconds")
#setup sero
servoP=machine.Pin(BoardInfo.servoPin, machine.Pin.OUT)
servo = machine.PWM(servoP,freq=50)

servoSet(closedPos)
for i in range(0,5):
    time.sleep(1)
    servoSet(openPos)
    time.sleep(1)
    servoSet(closedPos)
print("Servo Test Done")
print("Status Light Test - All Light Flash 10 Sec")
for i in range(0,5):
    time.sleep(1)
    lights(1)
    time.sleep(1)
    lights(0)
print("Status Light Test Done")
print("Input Test")
while True:
    #output=str(modeP.value())
    outputA ="Mode="+str(modeP.value())+"       Sensor="+str(senseP.value())+"         Man On="+str(manOnP.value())
    outputB="Man Off="+str(manOffP.value())+"    WIFI Enable="+str(wifiEnP.value())+"    Sensor Enable="+str(senseEnP.value())
    print(outputA)
    print(outputB)
    time.sleep_ms(1000)

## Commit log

2023-01-05 Added Hardware Information
    [BlastGate R2_2-B_Cu.gbr, BlastGate R2_2-B_Mask.gbr, BlastGate R2_2-B_Paste.gbr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]
2023-01-06 fix issue if wifi not enabled
    [main.py]
2023-01-08 add servo movement to ap mode
2023-01-20 hw revisions
    [BlastGateRev3_0.kicad_pcb, BlastGateRev3_0.kicad_sch]
2023-01-28 hardware revision,
    [BlastGateRev3_1.kicad_pcb, BlastGateRev3_1.kicad_sch]
2023-03-31 Add GC, Code Cleanup
    [BlastGateRev3_1.kicad_pcb]
2023-03-31 Add auto reboot at Midnight
    [boot.py, main.py]
